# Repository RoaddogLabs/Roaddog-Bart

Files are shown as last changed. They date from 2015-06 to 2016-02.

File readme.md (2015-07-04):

This is a Roaddog Bart i3 Rework 3D printer. This machine is a mashup
implemented from several designs including original designs.  Original
designs from Roaddog Labs Ltd are released per the Open Source Hardware
Association guidelines for open source hardware at
http://www.oshwa.org/definition/.

Material specific to the Bart components and documentation that is not
derived from other sources are released under the Creative Commons
Attribution 4.0 International license.

Where applicable, the license of any derived work will be posted as
well.

The original Prusa i3 single plate files
(https://github.com/josefprusa/Prusa3) from Josef Prusa licensed under
GPL v3.

The original i3 Rework
(https://github.com/eMotion-Tech/Prusai3_EINSTEIN_Reworked) printed
parts files from eMotion-Tech are released under GPL 2.0.

The original i3 Hephestos files
(https://github.com/bq/prusa-i3-hephestos/) from bq Department of
Innovation and Robotics are licensed under Creative Commons Attribution
4.0 Sharealike International.

The Graber i3(https://github.com/sgraber/Graber) is licensed under GPL
v3.0.

The original modified i3 X idler with adjustable belt tensioner from
ramkam (http://www.thingiverse.com/thing:393870) licensed under Creative
Commons Atribution-Sharealike, no version stated.

Marlin firmware (https://github.com/MarlinFirmware/Marlin) from Erik van
der Zalm licensed under GPL, no version stated.

The original direct drive extruder for Wilson/i3
(http://www.thingiverse.com/thing:501755) from mrice licensed under
Creative Commons Attribution- Share Alike license, no version stated.

Z coupler from Yet Another Prusa Mendel Z Coupling, by Nophead licensed under GPL, no version stated.
http://www.thingiverse.com/thing:9622

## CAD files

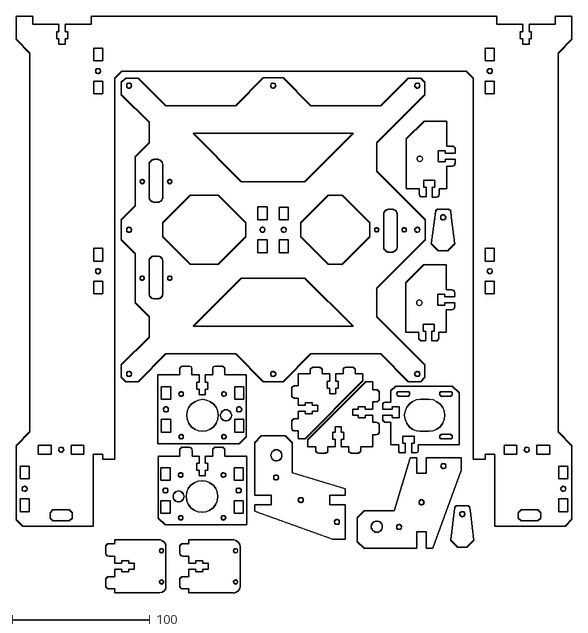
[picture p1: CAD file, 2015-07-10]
frame/bart main plate.dxf
402.9 x 418.3

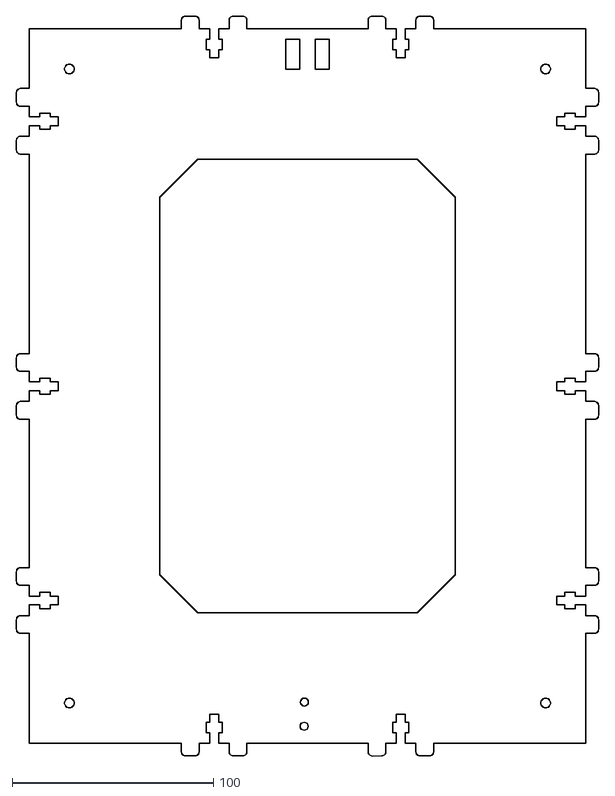
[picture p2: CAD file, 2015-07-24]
frame/bart bottom panel, Y motor mount mod.dxf
289.5 x 368.0

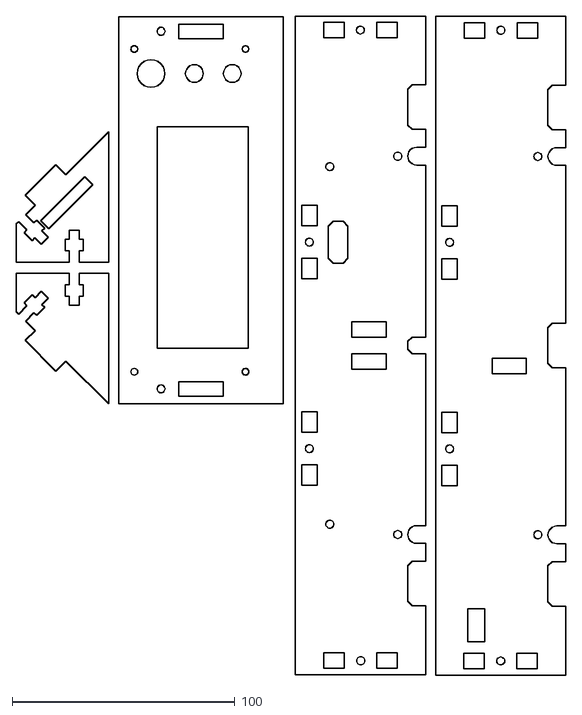
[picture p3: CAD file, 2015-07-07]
frame/laser cut Y motor mount parts depricated/bart ends laser cut Y motor mount.dxf
246.9 x 296.1

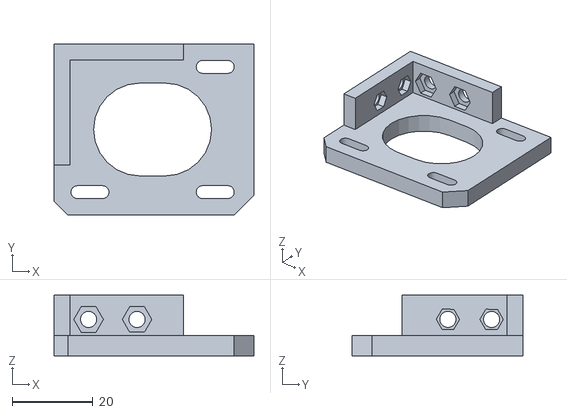
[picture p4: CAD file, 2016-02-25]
printed parts/bart Y motor mount v2.stl
49.5 x 42.4 x 15.0

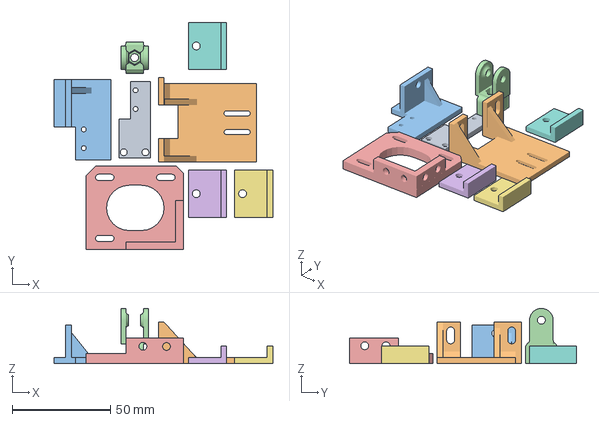
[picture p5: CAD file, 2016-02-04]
printed parts/production plates/plate 1 plain switch.amf
111.2 x 115.4 x 28.0 mm

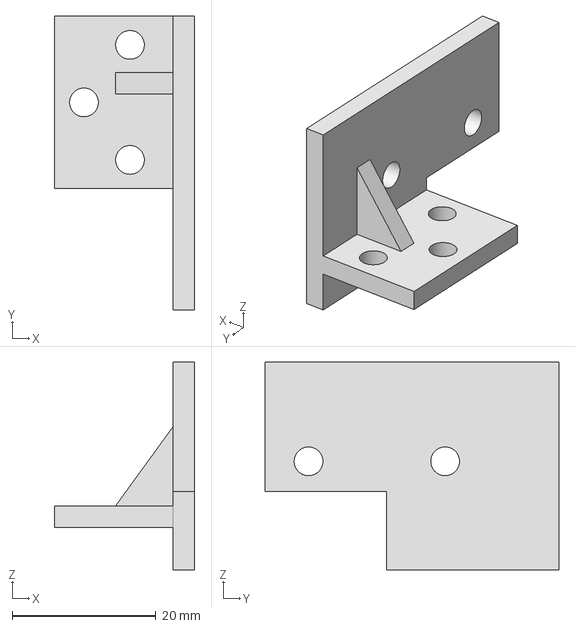
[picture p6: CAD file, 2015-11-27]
printed parts/source/Bart Y clip-endstop with rib.igs
19.5 x 40.9 x 28.9 mm

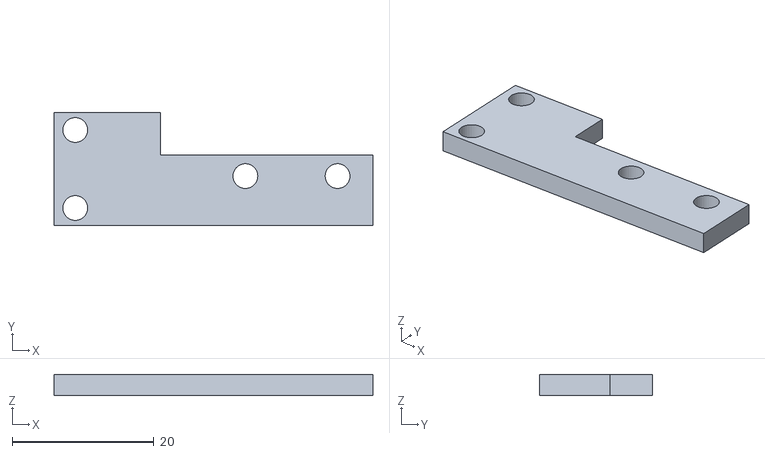
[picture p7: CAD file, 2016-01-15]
printed parts/plain switch endstop mounts/bart x endstop bracket plain switch v4.stl
45.0 x 16.0 x 3.00

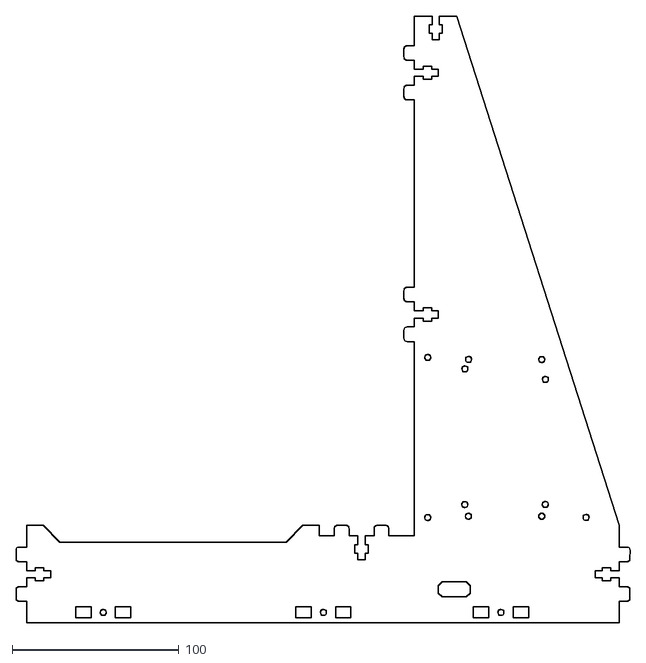
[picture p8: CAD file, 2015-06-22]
frame/bart side.dxf
368.1 x 363.9

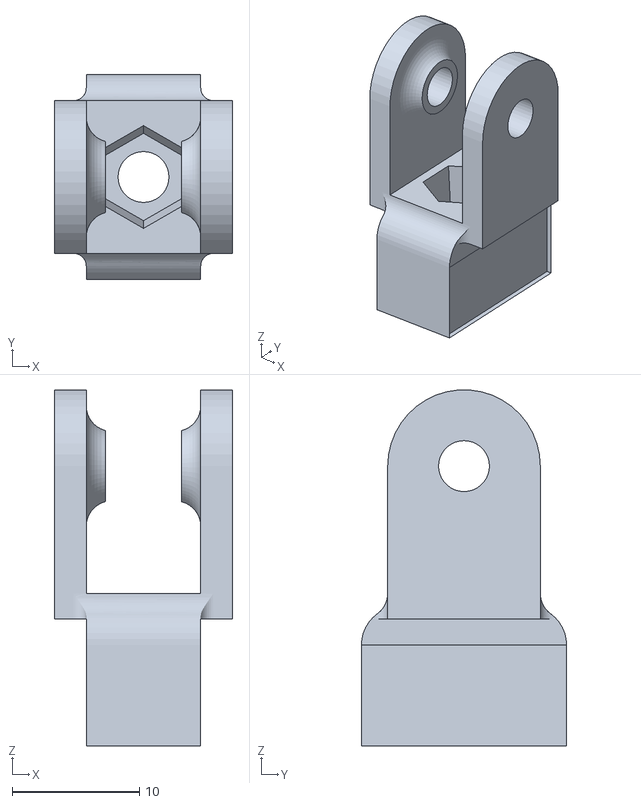
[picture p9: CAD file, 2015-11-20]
printed parts/bart x idler narrowed v2.stl
14.0 x 16.1 x 28.0

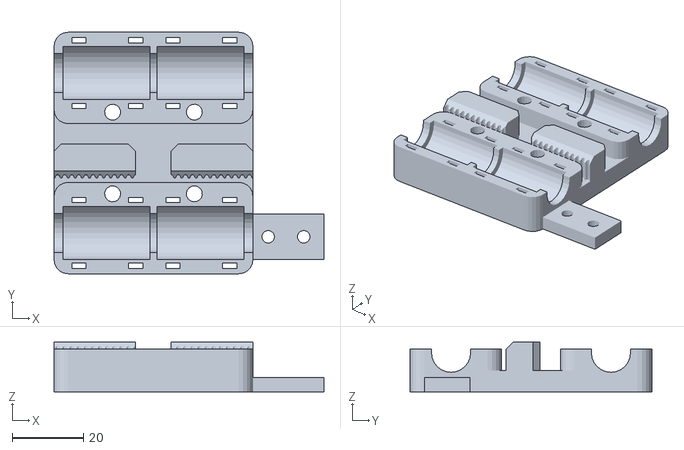
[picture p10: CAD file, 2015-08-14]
printed parts/bart x carriage 2 hole endstop trigger.stl
76.0 x 68.0 x 14.0

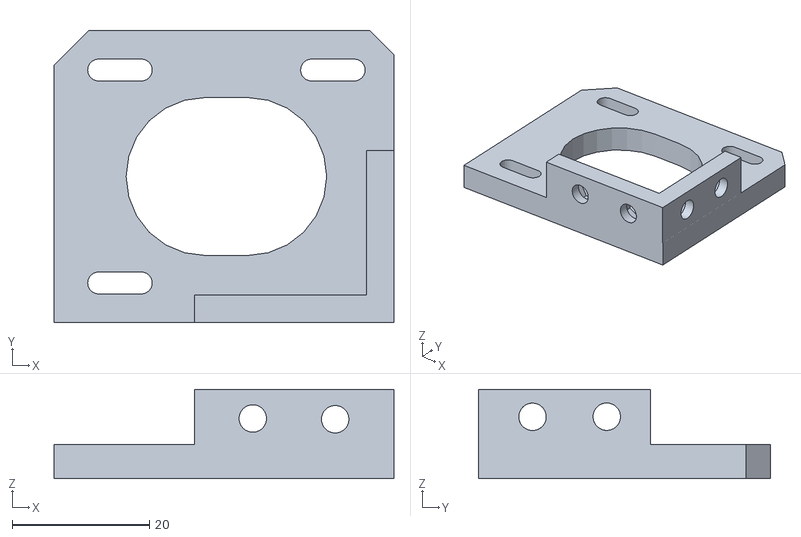
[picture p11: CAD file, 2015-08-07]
printed parts/bart Y motor mount rotated.stl
49.5 x 42.4 x 13.0

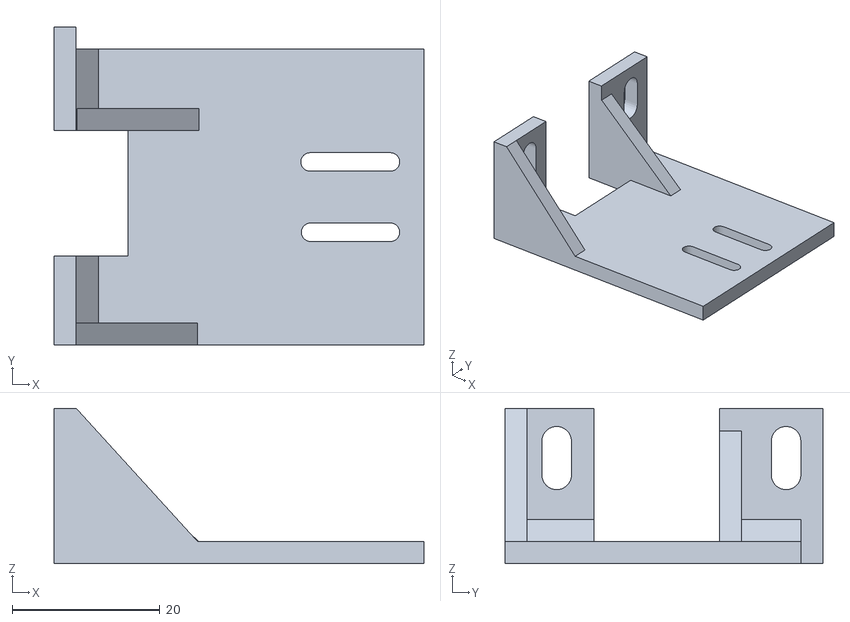
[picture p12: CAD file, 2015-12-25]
printed parts/plain switch endstop mounts/bart z endstop bracket plain switch v1.stl
50.0 x 43.0 x 21.0

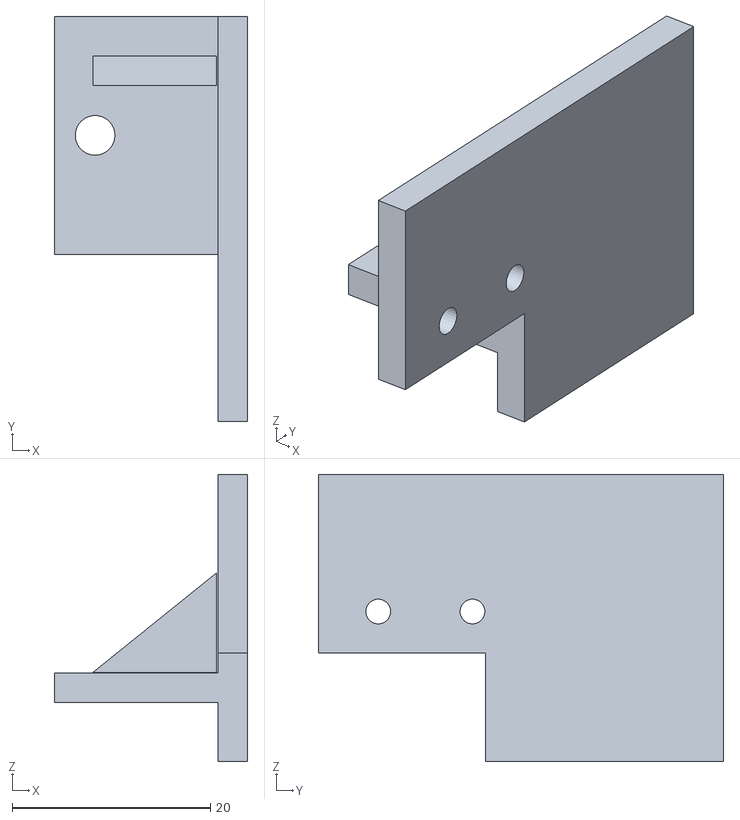
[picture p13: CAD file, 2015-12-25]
printed parts/plain switch endstop mounts/bart y end stop bracket plain switch v1.stl
19.5 x 40.9 x 28.9

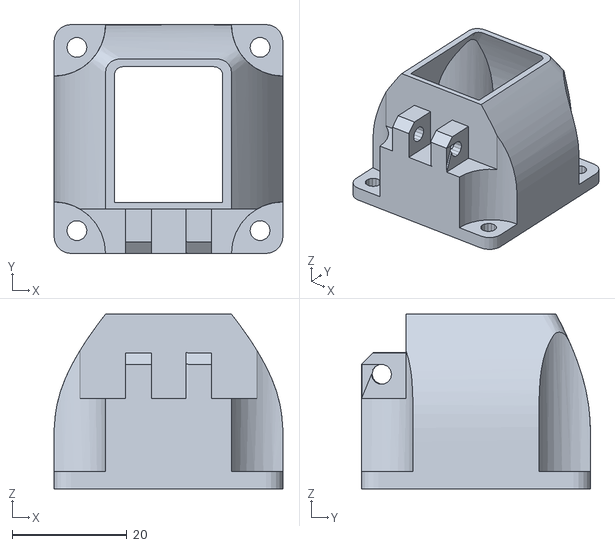
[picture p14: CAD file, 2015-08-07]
printed parts/bart extruder fan duct v2.stl
40.0 x 40.0 x 30.5

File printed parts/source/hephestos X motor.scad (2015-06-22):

//---------------------------------------------------------------
//--  Eje X izquierda.  (c) Antonio Castro Gómez
//---------------------------------------------------------------
//-- Released under the GPL license
//-- This file distributed with Roaddog Labs Ltd Bart i3 Rework
//---------------------------------------------------------------


module object1(scale) {polyhedron(
 points=[[4.721688e+001,-5.000000e+000,3.250000e+001],[4.721688e+001,-8.500000e+000,3.250000e+001],[4.173205e+001,-5.000000e+000,4.200000e+001],[4.173205e+001,-5.000000e+000,4.200000e+001],[4.721688e+001,-8.500000e+000,3.250000e+001],[4.000000e+001,-8.500000e+000,4.500000e+001],[4.173205e+001,-5.000000e+000,4.200000e+001],[4.000000e+001,-8.500000e+000,4.500000e+001],[4.000000e+001,-2.000000e+000,4.500000e+001],[4.000000e+001,-8.500000e+000,1.500000e+001],[4.721688e+001,-8.500000e+000,2.750000e+001],[4.000000e+001,-5.000000e+000,1.500000e+001],[4.000000e+001,-5.000000e+000,1.500000e+001],[4.721688e+001,-8.500000e+000,2.750000e+001],[4.721688e+001,-5.000000e+000,2.750000e+001],[5.450000e+001,-8.500000e+000,8.000000e+000],[4.758521e+001,-8.500000e+000,3.171010e+001],[4.781079e+001,-8.500000e+000,3.086824e+001],[5.450000e+001,-8.500000e+000,8.000000e+000],[4.781079e+001,-8.500000e+000,3.086824e+001],[4.788675e+001,-8.500000e+000,3.000000e+001],[5.450000e+001,-8.500000e+000,8.000000e+000],[4.788675e+001,-8.500000e+000,3.000000e+001],[4.781079e+001,-8.500000e+000,2.913176e+001],[5.450000e+001,-8.500000e+000,8.000000e+000],[4.781079e+001,-8.500000e+000,2.913176e+001],[4.758521e+001,-8.500000e+000,2.828990e+001],[5.450000e+001,-8.500000e+000,8.000000e+000],[4.758521e+001,-8.500000e+000,2.828990e+001],[4.721688e+001,-8.500000e+000,2.750000e+001],[5.450000e+001,-8.500000e+000,8.000000e+000],[4.721688e+001,-8.500000e+000,2.750000e+001],[4.000000e+001,-8.500000e+000,1.500000e+001],[5.450000e+001,-8.500000e+000,8.000000e+000],[4.000000e+001,-8.500000e+000,1.500000e+001],[4.000000e+001,-8.500000e+000,8.000000e+000],[5.450000e+001,-8.500000e+000,5.800000e+001],[4.000000e+001,-8.500000e+000,5.800000e+001],[4.000000e+001,-8.500000e+000,4.500000e+001],[5.450000e+001,-8.500000e+000,5.800000e+001],[4.000000e+001,-8.500000e+000,4.500000e+001],[4.721688e+001,-8.500000e+000,3.250000e+001],[5.450000e+001,-8.500000e+000,5.800000e+001],[4.721688e+001,-8.500000e+000,3.250000e+001],[4.758521e+001,-8.500000e+000,3.171010e+001],[5.450000e+001,-8.500000e+000,5.800000e+001],[4.758521e+001,-8.500000e+000,3.171010e+001],[5.450000e+001,-8.500000e+000,8.000000e+000],[4.721688e+001,-5.000000e+000,3.250000e+001],[4.173205e+001,-5.000000e+000,4.200000e+001],[7.535000e+001,-5.000000e+000,1.500000e+001],[4.721688e+001,-5.000000e+000,3.250000e+001],[7.535000e+001,-5.000000e+000,1.500000e+001],[4.758521e+001,-5.000000e+000,3.171010e+001],[7.535000e+001,-5.000000e+000,1.500000e+001],[4.000000e+001,-5.000000e+000,1.500000e+001],[4.721688e+001,-5.000000e+000,2.750000e+001],[7.535000e+001,-5.000000e+000,1.500000e+001],[4.721688e+001,-5.000000e+000,2.750000e+001],[4.758521e+001,-5.000000e+000,2.828990e+001],[7.535000e+001,-5.000000e+000,1.500000e+001],[4.758521e+001,-5.000000e+000,2.828990e+001],[4.781079e+001,-5.000000e+000,2.913176e+001],[7.535000e+001,-5.000000e+000,1.500000e+001],[4.781079e+001,-5.000000e+000,2.913176e+001],[4.788675e+001,-5.000000e+000,3.000000e+001],[7.535000e+001,-5.000000e+000,1.500000e+001],[4.788675e+001,-5.000000e+000,3.000000e+001],[4.781079e+001,-5.000000e+000,3.086824e+001],[7.535000e+001,-5.000000e+000,1.500000e+001],[4.781079e+001,-5.000000e+000,3.086824e+001],[4.758521e+001,-5.000000e+000,3.171010e+001],[8.000000e+001,-5.000000e+000,4.035000e+001],[9.383604e+001,-5.000000e+000,4.035000e+001],[9.250000e+001,-5.000000e+000,3.803590e+001],[8.000000e+001,-5.000000e+000,4.035000e+001],[9.250000e+001,-5.000000e+000,3.803590e+001],[8.188490e+001,-5.000000e+000,1.965000e+001],[8.000000e+001,-5.000000e+000,4.035000e+001],[8.188490e+001,-5.000000e+000,1.965000e+001],[8.000000e+001,-5.000000e+000,1.965000e+001],[8.000000e+001,-5.000000e+000,4.035000e+001],[8.000000e+001,-5.000000e+000,1.965000e+001],[7.535000e+001,-5.000000e+000,1.500000e+001],[8.000000e+001,-5.000000e+000,4.035000e+001],[7.535000e+001,-5.000000e+000,1.500000e+001],[4.173205e+001,-5.000000e+000,4.200000e+001],[8.000000e+001,-5.000000e+000,4.035000e+001],[4.173205e+001,-5.000000e+000,4.200000e+001],[8.000000e+001,-5.000000e+000,4.200000e+001],[4.721688e+001,-5.000000e+000,2.750000e+001],[4.721688e+001,-8.500000e+000,2.750000e+001],[4.758521e+001,-5.000000e+000,2.828990e+001],[4.758521e+001,-5.000000e+000,2.828990e+001],[4.721688e+001,-8.500000e+000,2.750000e+001],[4.758521e+001,-8.500000e+000,2.828990e+001],[4.758521e+001,-5.000000e+000,2.828990e+001],[4.758521e+001,-8.500000e+000,2.828990e+001],[4.781079e+001,-5.000000e+000,2.913176e+001],[4.781079e+001,-5.000000e+000,2.913176e+001],[4.758521e+001,-8.500000e+000,2.828990e+001],[4.781079e+001,-8.500000e+000,2.913176e+001],[4.781079e+001,-5.000000e+000,2.913176e+001],[4.781079e+001,-8.500000e+000,2.913176e+001],[4.788675e+001,-5.000000e+000,3.000000e+001],[4.788675e+001,-5.000000e+000,3.000000e+001],[4.781079e+001,-8.500000e+000,2.913176e+001],[4.788675e+001,-8.500000e+000,3.000000e+001],[4.788675e+001,-5.000000e+000,3.000000e+001],[4.788675e+001,-8.500000e+000,3.000000e+001],[4.781079e+001,-5.000000e+000,3.086824e+001],[4.781079e+001,-5.000000e+000,3.086824e+001],[4.788675e+001,-8.500000e+000,3.000000e+001],[4.781079e+001,-8.500000e+000,3.086824e+001],[4.781079e+001,-5.000000e+000,3.086824e+001],[4.781079e+001,-8.500000e+000,3.086824e+001],[4.758521e+001,-5.000000e+000,3.171010e+001],[4.758521e+001,-5.000000e+000,3.171010e+001],[4.781079e+001,-8.500000e+000,3.086824e+001],[4.758521e+001,-8.500000e+000,3.171010e+001],[4.758521e+001,-5.000000e+000,3.171010e+001],[4.758521e+001,-8.500000e+000,3.171010e+001],[4.721688e+001,-5.000000e+000,3.250000e+001],[4.721688e+001,-5.000000e+000,3.250000e+001],[4.758521e+001,-8.500000e+000,3.171010e+001],[4.721688e+001,-8.500000e+000,3.250000e+001],[4.000000e+001,5.000000e+000,1.500000e+001],[4.721688e+001,5.000000e+000,2.750000e+001],[4.000000e+001,8.500000e+000,1.500000e+001],[4.000000e+001,8.500000e+000,1.500000e+001],[4.721688e+001,5.000000e+000,2.750000e+001],[4.721688e+001,8.500000e+000,2.750000e+001],[4.173205e+001,5.000000e+000,4.200000e+001],[4.000000e+001,2.000000e+000,4.500000e+001],[4.000000e+001,8.500000e+000,4.500000e+001],[4.721688e+001,8.500000e+000,3.250000e+001],[4.173205e+001,5.000000e+000,4.200000e+001],[4.000000e+001,8.500000e+000,4.500000e+001],[4.721688e+001,5.000000e+000,3.250000e+001],[4.173205e+001,5.000000e+000,4.200000e+001],[4.721688e+001,8.500000e+000,3.250000e+001],[8.000000e+001,5.000000e+000,4.035000e+001],[9.250000e+001,5.000000e+000,3.803590e+001],[9.383604e+001,5.000000e+000,4.035000e+001],[7.535000e+001,5.000000e+000,1.500000e+001],[8.000000e+001,5.000000e+000,1.965000e+001],[8.000000e+001,5.000000e+000,4.035000e+001],[7.535000e+001,5.000000e+000,1.500000e+001],[8.000000e+001,5.000000e+000,4.035000e+001],[8.000000e+001,5.000000e+000,4.200000e+001],[7.535000e+001,5.000000e+000,1.500000e+001],[8.000000e+001,5.000000e+000,4.200000e+001],[4.173205e+001,5.000000e+000,4.200000e+001],[7.535000e+001,5.000000e+000,1.500000e+001],[4.173205e+001,5.000000e+000,4.200000e+001],[4.721688e+001,5.000000e+000,3.250000e+001],[7.535000e+001,5.000000e+000,1.500000e+001],[4.721688e+001,5.000000e+000,3.250000e+001],[4.758521e+001,5.000000e+000,3.171010e+001],[7.535000e+001,5.000000e+000,1.500000e+001],[4.758521e+001,5.000000e+000,3.171010e+001],[4.781079e+001,5.000000e+000,3.086824e+001],[7.535000e+001,5.000000e+000,1.500000e+001],[4.781079e+001,5.000000e+000,3.086824e+001],[4.788675e+001,5.000000e+000,3.000000e+001],[7.535000e+001,5.000000e+000,1.500000e+001],[4.788675e+001,5.000000e+000,3.000000e+001],[4.781079e+001,5.000000e+000,2.913176e+001],[7.535000e+001,5.000000e+000,1.500000e+001],[4.781079e+001,5.000000e+000,2.913176e+001],[4.758521e+001,5.000000e+000,2.828990e+001],[7.535000e+001,5.000000e+000,1.500000e+001],[4.758521e+001,5.000000e+000,2.828990e+001],[4.721688e+001,5.000000e+000,2.750000e+001],[7.535000e+001,5.000000e+000,1.500000e+001],[4.721688e+001,5.000000e+000,2.750000e+001],[4.000000e+001,5.000000e+000,1.500000e+001],[8.000000e+001,5.000000e+000,1.965000e+001],[9.389810e+001,5.000000e+000,1.965000e+001],[9.330056e+001,5.000000e+000,2.050570e+001],[8.000000e+001,5.000000e+000,1.965000e+001],[9.330056e+001,5.000000e+000,2.050570e+001],[9.286034e+001,5.000000e+000,2.145200e+001],[8.000000e+001,5.000000e+000,1.965000e+001],[9.286034e+001,5.000000e+000,2.145200e+001],[9.259077e+001,5.000000e+000,2.246027e+001],[8.000000e+001,5.000000e+000,1.965000e+001],[9.259077e+001,5.000000e+000,2.246027e+001],[9.250000e+001,5.000000e+000,2.350000e+001],[8.000000e+001,5.000000e+000,1.965000e+001],[9.250000e+001,5.000000e+000,2.350000e+001],[9.250000e+001,5.000000e+000,3.803590e+001],[8.000000e+001,5.000000e+000,1.96
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

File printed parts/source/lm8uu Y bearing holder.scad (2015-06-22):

// Prusa i3 lm8uu holder

$fn=0;
$fa=0.1;
$fs=0.3;

bearing_diameter=15;
bearing_length=24;
wall_thickness=2;
hole_spacing=20;
hole_diameter=3.5; //M3
screw_head_diameter=6;

module bearing_holder()
{
  difference(){
  rotate([0,90,0])
  translate([-bearing_diameter/2-wall_thickness-2, 0, 0])
    cylinder(h=bearing_length, r=bearing_diameter/2 +wall_thickness, center=true);

  rotate([0,90,0])
  translate([-bearing_diameter/2-wall_thickness-2,0,0])
    cylinder(h=bearing_length+1, r=bearing_diameter/2, center=true);

  translate([0,0,bearing_diameter])
  cube([bearing_length+2, 4, 15], true);

  }
} 

module mounting_plate()
{
  difference(){
  translate([0,0,2])
  cube ([bearing_length,hole_spacing+(hole_diameter*2) +4,4], true);

  rotate([0,90,0])
  translate([-bearing_diameter/2-wall_thickness,0,0])
    cylinder(h=bearing_length+1, r=bearing_diameter/2, center=true);
  for (i=[-hole_spacing/2, hole_spacing/2]){
    translate([0,i,0])
    cylinder(h=10,r=hole_diameter/2, center=true);
translate([0,i,5+2])
    cylinder(h=10,r=screw_head_diameter/2, center=true);
    }
  }
  
}
difference(){
  union(){
    mounting_plate();
    bearing_holder();
    }
 for (i=[-hole_spacing/2, hole_spacing/2]){
    
  translate([0,i,15+4])
    cylinder(h=30,r=screw_head_diameter/2, center=true);
    }

}

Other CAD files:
printed parts/bart y clip-endstop bracket with rib.stl
printed parts/bart y idler narrowed.stl
printed parts/bart z endstop bracket.stl
printed parts/bart x endstop block 2 hole.stl
printed parts/source/nophead z coupler.scad
Marlin Bart RAMPS/Bart-RAMPS/Documentation/Logo/Marlin Logo.dxf
printed parts/bart X end idler.stl
printed parts/bart X end.stl
printed parts/bart X motor end.stl
printed parts/bart Y clip single hole mount.stl
printed parts/bart extruder motor on left.stl
printed parts/lm8uu Y bearing holder rotated.stl
printed parts/lm8uu Y bearing holder.stl
printed parts/plain switch endstop mounts/bart x endstop bracket plain switch v1.stl
printed parts/plain switch endstop mounts/bart x endstop bracket plain switch v2.stl
printed parts/plain switch endstop mounts/bart x endstop bracket plain switch v3.stl
printed parts/source/X endstop block.f3d
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

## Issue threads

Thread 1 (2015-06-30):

extend Z endstop bracket

RoaddogLabs, 2015-06-30:
add 5 mm to top of Z endstop bracket
change endstop mounting holes to slots so they can be adjusted

Closed 2015-06-30.

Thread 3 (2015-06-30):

fix fan to extruder mount play

RoaddogLabs, 2015-06-30:
widen the fan mount on the extruder

RoaddogLabs, 2015-07-10:
print wildon fan shourd first to see it this resolves the issue

RoaddogLabs, 2015-08-02:
modded rework fan duct

Closed 2015-08-02.

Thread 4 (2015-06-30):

X carriage endstop holder mount

RoaddogLabs, 2015-06-30:
lengthen X carraige endstop holder mount and add hole to both the X carraige and the stop block

Closed 2015-07-10.

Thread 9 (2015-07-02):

test 3 point bed mount/leveling

RoaddogLabs, 2015-07-02:
watch for cable routing, glass clip clearance on sides

RoaddogLabs, 2015-07-04:
worked well, will leave on as option in kit

Closed 2015-07-04.

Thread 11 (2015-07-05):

change rear bed level screw to spacer from spring

RoaddogLabs, 2015-07-05:

RoaddogLabs, 2015-07-17:
design reverts to 4 point bed mount

Closed 2015-07-17.

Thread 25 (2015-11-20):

Marlin won't compile with U8glib 1.18.1

RoaddogLabs, 2015-11-20:
lots of warnings barked, 1.18.1 exits on file not found error

RoaddogLabs, 2015-11-28:
update ide to current version, fixed but with warnings
use prior version from google code repo not current version
do not build against 1.18.1

Closed 2015-11-28.

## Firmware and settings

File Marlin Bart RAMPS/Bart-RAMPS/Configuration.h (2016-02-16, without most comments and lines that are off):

#define CONFIGURATION_H
#include "boards.h"
#define STRING_VERSION_CONFIG_H __DATE__ " " __TIME__ // build date and time
#define STRING_CONFIG_H_AUTHOR "(Bart RAMPS)" // Who made the changes.
#define SERIAL_PORT 0
#define BAUDRATE 115200
  #define MOTHERBOARD BOARD_RAMPS_13_EFB
#define CUSTOM_MENDEL_NAME "Roaddog Bart"
#define EXTRUDERS 1
#define POWER_SUPPLY 1
#define TEMP_SENSOR_0 5
#define TEMP_SENSOR_1 0
#define TEMP_SENSOR_2 0
#define TEMP_SENSOR_BED 1
#define MAX_REDUNDANT_TEMP_SENSOR_DIFF 10
#define TEMP_RESIDENCY_TIME 10  // (seconds)
#define TEMP_HYSTERESIS 3       // (degC) range of +/- temperatures considered "close" to the target one
#define TEMP_WINDOW     1       // (degC) Window around target to start the residency timer x degC early.
#define HEATER_0_MINTEMP 5
#define HEATER_1_MINTEMP 5
#define HEATER_2_MINTEMP 5
#define BED_MINTEMP 5
#define HEATER_0_MAXTEMP 275
#define HEATER_1_MAXTEMP 275
#define HEATER_2_MAXTEMP 275
#define BED_MAXTEMP 150
#define PIDTEMP
#define BANG_MAX 255 // limits current to nozzle while in bang-bang mode; 255=full current
#define PID_MAX BANG_MAX // limits current to nozzle while PID is active (see PID_FUNCTIONAL_RANGE below); 255=full current
  #define PID_FUNCTIONAL_RANGE 10 // If the temperature difference between the target temperature and the actual temperature
  #define PID_INTEGRAL_DRIVE_MAX PID_MAX  //limit for the integral term
  #define K1 0.95 //smoothing factor within the PID
  #define PID_dT ((OVERSAMPLENR * 10.0)/(F_CPU / 64.0 / 256.0)) //sampling period of the temperature routine
    #define  DEFAULT_Kp 30.9
    #define  DEFAULT_Ki 1.96
    #define  DEFAULT_Kd 121.49
#define MAX_BED_POWER 255 // limits duty cycle to bed; 255=full current
#define PREVENT_DANGEROUS_EXTRUDE
#define PREVENT_LENGTHY_EXTRUDE
#define EXTRUDE_MINTEMP 170
#define EXTRUDE_MAXLENGTH (X_MAX_LENGTH+Y_MAX_LENGTH) //prevent extrusion of very large distances.
#define ENDSTOPPULLUPS // Comment this out (using // at the start of the line) to disable the endstop pullup resistors
  #define ENDSTOPPULLUP_XMAX
  #define ENDSTOPPULLUP_YMAX
  #define ENDSTOPPULLUP_ZMAX
  #define ENDSTOPPULLUP_XMIN
  #define ENDSTOPPULLUP_YMIN
  #define ENDSTOPPULLUP_ZMIN
const bool X_MIN_ENDSTOP_INVERTING = true; // set to true to invert the logic of the endstop.
const bool Y_MIN_ENDSTOP_INVERTING = true; // set to true to invert the logic of the endstop.
const bool Z_MIN_ENDSTOP_INVERTING = true; // set to true to invert the logic of the endstop.
const bool X_MAX_ENDSTOP_INVERTING = true; // set to true to invert the logic of the endstop.
const bool Y_MAX_ENDSTOP_INVERTING = true; // set to true to invert the logic of the endstop.
const bool Z_MAX_ENDSTOP_INVERTING = true; // set to true to invert the logic of the endstop.
#if defined(COREXY) && !defined(DISABLE_MAX_ENDSTOPS)
  #define DISABLE_MAX_ENDSTOPS
#endif
#define X_ENABLE_ON 0
#define Y_ENABLE_ON 0
#define Z_ENABLE_ON 0
#define E_ENABLE_ON 0 // For all extruders
#define DISABLE_X false
#define DISABLE_Y false
#define DISABLE_Z false
#define DISABLE_E false // For all extruders
#define DISABLE_INACTIVE_EXTRUDER true //disable only inactive extruders and keep active extruder enabled
#define INVERT_X_DIR true    // for Mendel set to false, for Orca set to true
#define INVERT_Y_DIR false    // for Mendel set to true, for Orca set to false
#define INVERT_Z_DIR true     // for Mendel set to false, for Orca set to true
#define INVERT_E0_DIR false   // for direct drive extruder v9 set to true, for geared extruder set to false
#define INVERT_E1_DIR false    // for direct drive extruder v9 set to true, for geared extruder set to false
#define INVERT_E2_DIR false   // for direct drive extruder v9 set to true, for geared extruder set to false
#define X_HOME_DIR 1
#define Y_HOME_DIR -1
#define Z_HOME_DIR -1
#define min_software_endstops true // If true, axis won't move to coordinates less than HOME_POS.
#define max_software_endstops true  // If true, axis won't move to coordinates greater than the defined lengths below.
#define X_MAX_POS 205
#define X_MIN_POS 0
#define Y_MAX_POS 205
#define Y_MIN_POS 0
#define Z_MAX_POS 200
#define Z_MIN_POS 0
#define X_MAX_LENGTH (X_MAX_POS - X_MIN_POS)
#define Y_MAX_LENGTH (Y_MAX_POS - Y_MIN_POS)
#define Z_MAX_LENGTH (Z_MAX_POS - Z_MIN_POS)
#define Z_PROBE_REPEATABILITY_TEST  // If not commented out, Z-Probe Repeatability test will be included if Auto Bed Leveling is Enabled.
#define MANUAL_X_HOME_POS 0
#define MANUAL_Y_HOME_POS 0
#define MANUAL_Z_HOME_POS 0
#define NUM_AXIS 4 // The axis order in all axis related arrays is X, Y, Z, E
#define HOMING_FEEDRATE {50*60, 50*60, 3*60, 0}  // set the homing speeds (mm/min)
#define DEFAULT_AXIS_STEPS_PER_UNIT   {80,80,4000,95}  //settings for Bart direct drive extruder
#define DEFAULT_MAX_FEEDRATE          {500, 500, 2, 25}    // (mm/sec)
#define DEFAULT_MAX_ACCELERATION      {4000,4000,10,10000}    // X, Y, Z, E maximum start speed for accelerated moves. E default values are good for Skeinforge 40+, for older versions raise them a lot.
#define DEFAULT_ACCELERATION          1000    // X, Y, Z and E max acceleration in mm/s^2 for printing moves default was 3000
#define DEFAULT_RETRACT_ACCELERATION  3000   // X, Y, Z and E max acceleration in mm/s^2 for retracts
#define DEFAULT_XYJERK                6.0    // (mm/sec) // default was 10.0
#define DEFAULT_ZJERK                 0.4     // (mm/sec)
#define DEFAULT_EJERK                 5.0    // (mm/sec)
#define CUSTOM_M_CODES
  #define CUSTOM_M_CODE_SET_Z_PROBE_OFFSET 851
  #define Z_PROBE_OFFSET_RANGE_MIN -15
  #define Z_PROBE_OFFSET_RANGE_MAX -5
#define PLA_PREHEAT_HOTEND_TEMP 180
#define PLA_PREHEAT_HPB_TEMP 70
#define PLA_PREHEAT_FAN_SPEED 255   // Insert Value between 0 and 255
#define ABS_PREHEAT_HOTEND_TEMP 240
#define ABS_PREHEAT_HPB_TEMP 100
#define ABS_PREHEAT_FAN_SPEED 255   // Insert Value between 0 and 255
#define SDSUPPORT // Enable SD Card Support in Hardware Console
#define REPRAP_DISCOUNT_FULL_GRAPHIC_SMART_CONTROLLER
 #define DOGLCD
 #define U8GLIB_ST7920
 #define REPRAP_DISCOUNT_SMART_CONTROLLER
 #define ULTIPANEL
 #define NEWPANEL
  #define SDSUPPORT
  #define ULTRA_LCD
    #define LCD_WIDTH 20
    #define LCD_HEIGHT 5
#  define DEFAULT_LCD_CONTRAST 32
#define SOFT_PWM_SCALE 0
#define FILAMENT_SENSOR_EXTRUDER_NUM	0  //The number of the extruder that has the filament sensor (0,1,2)
#define MEASUREMENT_DELAY_CM			14  //measurement delay in cm.  This is the distance from filament sensor to middle of barrel
#define DEFAULT_NOMINAL_FILAMENT_DIA  1.75  //Enter the diameter (in mm) of the filament generally used (3.0 mm or 1.75 mm) - this is then used in the slicer software.  Used for sensor reading validation
#define MEASURED_UPPER_LIMIT          3.30  //upper limit factor used for sensor reading validation in mm
#define MEASURED_LOWER_LIMIT          1.90  //lower limit factor for sensor reading validation in mm
#define MAX_MEASUREMENT_DELAY			20  //delay buffer size in bytes (1 byte = 1cm)- limits maximum measurement delay allowable (must be larger than MEASUREMENT_DELAY_CM  and lower number saves RAM)
#define DEFAULT_MEASURED_FILAMENT_DIA  DEFAULT_NOMINAL_FILAMENT_DIA  //set measured to nominal initially
#include "Configuration_adv.h"
#include "thermistortables.h"

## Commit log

2015-06-22 BOM NOT COMPLETE
2015-06-22 update gitignore
    don’t track .dwg, .fff, .factory, .gcode, .fabbproject
2015-06-22 update z endstop bracket to v4
    [bart Z endstop bracket.stl, bart z endstop bracket v4.stl]
2015-06-22 update z endstop bracket
    [bart z endstop bracket.stl]
2015-06-22 added z endstop bracket source
    [bart z endstop bracket v4.ipt]
2015-06-22 update frame for 624 Y idler bearing parts
    [bart main plate.dxf]
2015-07-04 add Nophead z coupler
    [nophead z coupler.scad]
2015-07-07 change end plates
    rod mount holes/clip and bed cable passthrough
    [bart ends.dxf]
2015-07-07 Z motor mount support mod
    trim nubs on Z motor mount support
    [bart main plate.dxf]
2015-07-08 x carriage mod
    [bart X carriage.stl]
2015-07-08 y clip single hole
    [bart Y clip single hole mount.stl]
2015-07-08 new z endstop bracket
    [bart z endstop bracket.stl]
2015-07-08 new x carriage source
    [bart X carriage w-endstop mods.ipt]
2015-07-08 new z endstop bracker source
    [bart z endstop bracket v9.ipt]
2015-07-08 x endstop black 2 hole
    [bart X endstop block.stl, x endstop block.stl]
2015-07-08 y clip one hole
    [bart Y clip.stl]
2015-07-08 clearing old files
    [bart X carriage 1 hole.ipt, bart Y clip 3 hole.ipt]
2015-07-08 x ensstop block source
    [x endstop block 2 holes.f3d]
2015-07-10 add Y belt holder mod
    lowered mounting holes due to Y idler bearing mod so belts tracking is
    parallel
    [bart main plate.dxf]
2015-07-17 added Bart name to lcd display/sd reader
    [Configuration.h]
2015-07-17 updated Z endstop
    [bart z endstop bracket v12.ipt, bart z endstop bracket v4.ipt, bart z endstop bracket v9.ipt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]
2015-07-17 updated Y endstop
    [bart Y endstop bracket.ipt]
2015-07-18 y endstop re commit
    [bart y endstop v2.ipt]
2015-07-18 y endstop source commit
    [bart Y endstop bracket-clip.stl, bart y endstop v2.ipt]
2015-07-24 added printed Y motor mount
    [Y motor mount.ipt, bart Y motor mount rotated.stl]
2015-07-24 revised Z coupler stl
    [bart z coupler.stl]
2015-07-24 Y motor mount mods
    [bart bottom laser cut Y motor mount.dxf, bart bottom panel, Y motor mount mod.dxf, bart ends laser cut Y motor mount.dxf]
2015-07-27 update z coupler inside dims
    [bart z coupler v2.stl]
2015-08-07 print cooling fan duct updated
    [bart extruder fan duct v2.stl]
2015-08-07 y idler updated
    [bart y idler narrowed.stl]
2015-08-07 y motor stl fixed
    [bart Y motor mount rotated.stl]
2015-08-07 removed coupler
    [bart z coupler v2.stl, bart z coupler.stl]
2015-08-07 updated BOM
2015-08-10 added wilson extruder source
    [extruder-direct-drive.skp]
2015-08-14 update X carriage and sync files
    [bart X carriage.stl, bart x carriage 2 hole endstop trigger.ipt, bart x carriage 2 hole endstop trigger.stl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]
2015-08-18 added y clip-endstop stl
    [bart Y endstop bracket-clip.stl]
2015-08-19 BOM RTM
    audited BOM counts
2015-08-20 fix string error in display options
    [Configuration.h]
2015-11-20 update Marlin builds for current release
    builds against ide 1.6.6 with u8glib 1.13.1 only
    [Configuration.h, Configuration_adv.h, Marlin Logo.dxf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]
2015-11-20 parts update
    x idler and fan duct
    [bart extruder fan duct.stl, bart x idler narrowed v2.stl]
2015-11-27 y endstop mount-clip with rib support
    [Bart Y clip-endstop with rib.igs, bart Y clip-enstopmount with rib.f3d, bart Y endstop bracket-clip.stl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]
2015-12-10 fix z homing rate issue
    z homing acceleration and feed rate calcs did not compile properly
    under Arduino 1.6.6
    [Configuration.h]
2015-12-25 added plain endstop switch brackets
    [bart x endstop bracket plain switch v1.ipt, bart x endstop bracket plain switch v1.stl, bart y end stop bracket plain switch v1.ipt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]
2015-12-25 update frame cut parts
    [bart bottom laser cut Y motor mount.dxf, bart ends laser cut Y motor mount.dxf]
2016-01-15 update plain switch brackets
    [bart Y motor mount v2.ipt, bart x endstop bracket plain switch v2.f3d, bart x endstop bracket plain switch v2.stl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]
2016-01-15 rename .ino file to reflect machine name instead of generic Marlin
2016-02-04 update bom for new x end stop mount
2016-02-04 revised dir structure/ compiles under 1.6.7
    [Configuration.h, Configuration_adv.h, Marlin Logo.dxf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]
2016-02-16 fixed SD support config
    latest update did not define SD support
    [Configuration.h]
2016-02-25 update Y motor mount
    [bart Y motor mount v2 .f3d, bart Y motor mount v2.stl]
